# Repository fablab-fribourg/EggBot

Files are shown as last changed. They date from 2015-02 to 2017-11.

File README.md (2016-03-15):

# EggBot
All you need to make your own EggBot.

This repository contains the Arduino code and a computer application to print files.

## Licence

 * Hardware is under Creative Commons Attribution-ShareAlike 3.0
 * Arduino code is under GNU GPL
 * The GcodeSender (computer application) application is under MIT Licence
 
## Electronics 
 * 1x Arduino uno
 * 1x CNC shield for Arduino UNO
 * 2x A4988 Stepper driver
 * 2x Nema 17 Stepper motor
 * 1x mini servo
 * 1x 12 volt power supply (min 1A)
 * 6x Jumpers

##Mechanic
 * 8x	Nuts M4
 * 1x	Threaded shaft M4 100mm
 * 8x	Hex head screws M4 x20mm
 * 20x	Nuts M3
 * 16x	Screws M3 x 8mm
 * 12x	Screws M3 x 16mm
 * 8x	Washers M3
 * 1x	Nail diam 1 or 2mm
 * 1x	Spring ~M4

## Computer application

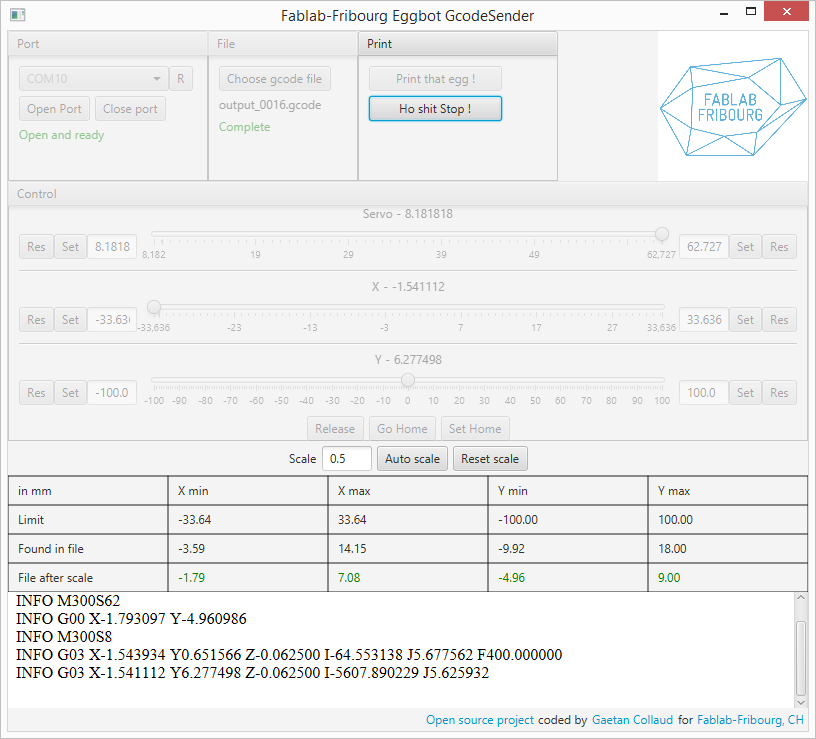
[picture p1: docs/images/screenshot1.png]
GcodeSender


**Steps to print a file**

* start the application
* choose and open the port where the arduino is connected (donc forget to upload the Arduino sketch first)
* choose the file you want to print 
  * this is a simple GCode file
  * you can convert an image with the last version of inkscape ([demo](https://www.youtube.com/watch?v=4jYKMAjzK3A))
* *[Optional]* adjust the limits
* *[Optional]* adjust the scale
* *[Optional]* define home
* "Print that egg"

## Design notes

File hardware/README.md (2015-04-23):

# EggBot Hardware

In this directory you will find the lasercut file to make you own eggbot.

Use the eggbot-frame-fablab-fribourg.svg if you want our upgraded version. Otherwise use the orignal files.

## Licence



Everything in this directory is under Creative Commons Attribution-ShareAlike 3.0.

Original work is from [Christoph Reinhardt](http://www.christophreinhardt.ch/)

Changes made by [Michel Collaud](http://www.easyloc.ch/) :
 * machine height
 * pen support
 * electronic position
 * holes adjustments
 * laser cutter optimisations

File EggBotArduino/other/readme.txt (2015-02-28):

v0.1

This is the firmware for an EggBot-style SphereBot.
The firmware directly interprets GCode send over the serial port.

There will be more information on the SphereBot at http://pleasantsoftware.com/developer/3d (in the near future...)

!!!!!!!!
This sketch needs the following non-standard libraries (install them in the Arduino library directory):
SoftwareServo: http://www.arduino.cc/playground/ComponentLib/Servo
TimerOne: http://www.arduino.cc/playground/Code/Timer1
!!!!!!!!

Copyright 2011 by Eberhard Rensch <http://pleasantsoftware.com/developer/3d>

This program is free software: you can redistribute it and/or modify
it under the terms of the GNU General Public License as published by
the Free Software Foundation, either version 3 of the License, or
(at your option) any later version.

This program is distributed in the hope that it will be useful,
but WITHOUT ANY WARRANTY; without even the implied warranty of
MERCHANTABILITY or FITNESS FOR A PARTICULAR PURPOSE.  See the
GNU General Public License for more details.

You should have received a copy of the GNU General Public License
along with this program.  If not, see <http://www.gnu.org/licenses/>

Part of this code is based on/inspired by the Helium Frog Delta Robot Firmware
by Martin Price <http://www.HeliumFrog.com>

To create tags File: ctags --langmap="C++:+.pde" S*

GCode commands:

G90	Absolut modus
G91	Icremental modus:

M300S0	Servo 0 degree
M300S90	Servo 90 degree

M18	Stepper off

G0X0Y40	Rapid movement (pen 0mm, rotation 40mm)
G1X40Y0 Slower movement (pen 40mm, rotation 0mm)
G1Y10F660 Movement with feed 660mm/s (rotation 10mm)

;	Comment
( .. )	Comment

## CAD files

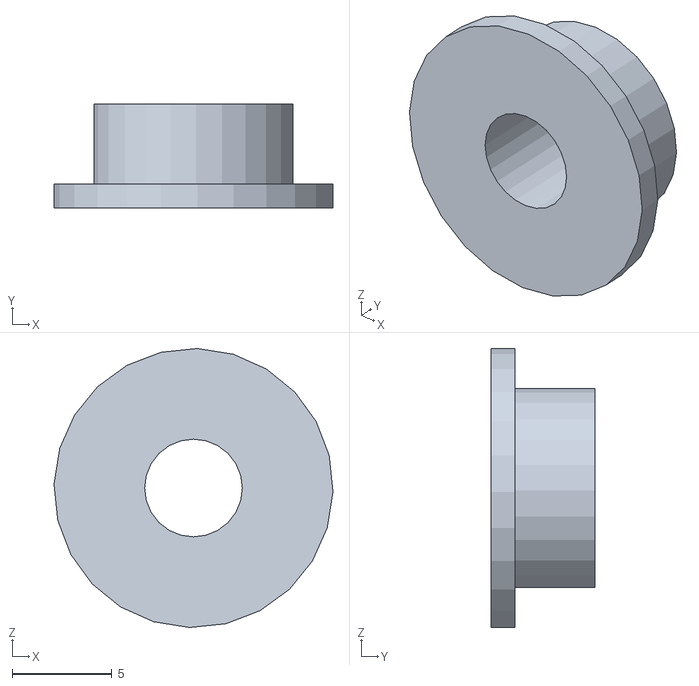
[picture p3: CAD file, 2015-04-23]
hardware/3d_printer/christophreinhardt/douille.stl
14.0 x 5.20 x 14.0

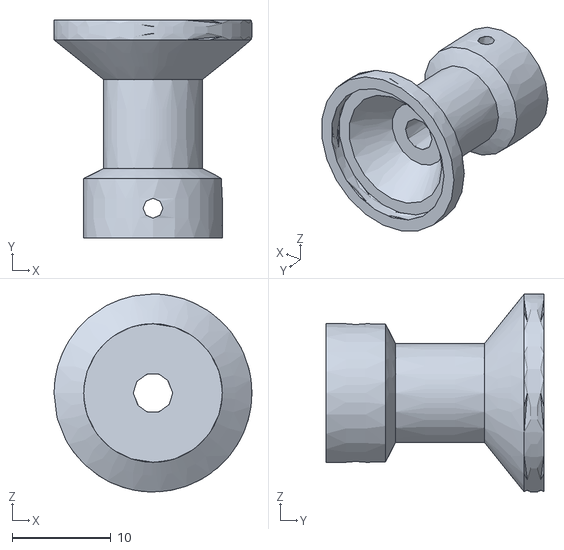
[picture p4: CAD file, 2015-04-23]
hardware/3d_printer/Michel/SupportRondelleCaoutchouc.stl
20.0 x 22.0 x 20.0

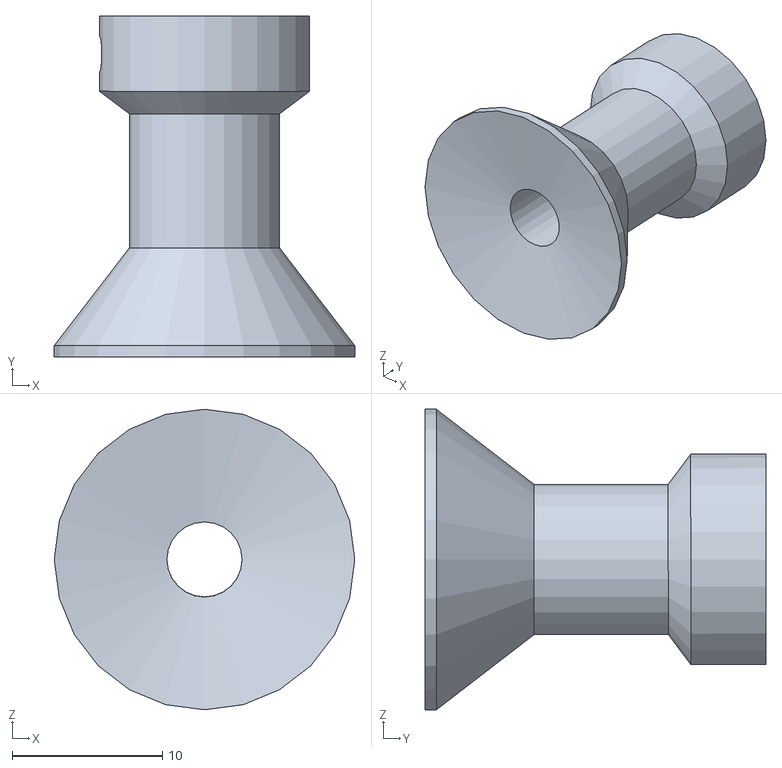
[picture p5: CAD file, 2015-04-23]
hardware/3d_printer/christophreinhardt/supportoeuf.stl
20.0 x 22.7 x 20.0

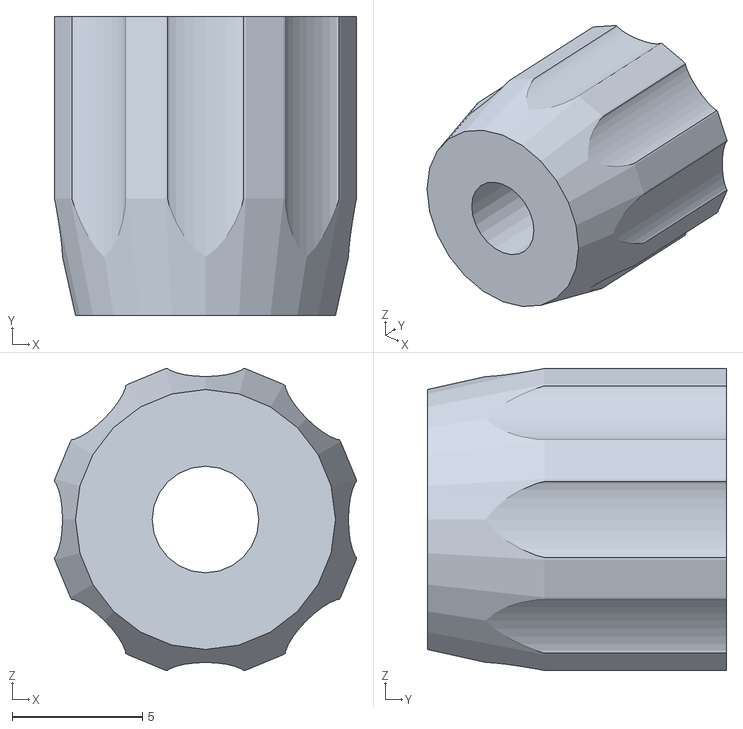
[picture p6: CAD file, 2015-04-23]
hardware/3d_printer/christophreinhardt/M4.stl
11.6 x 11.5 x 11.6

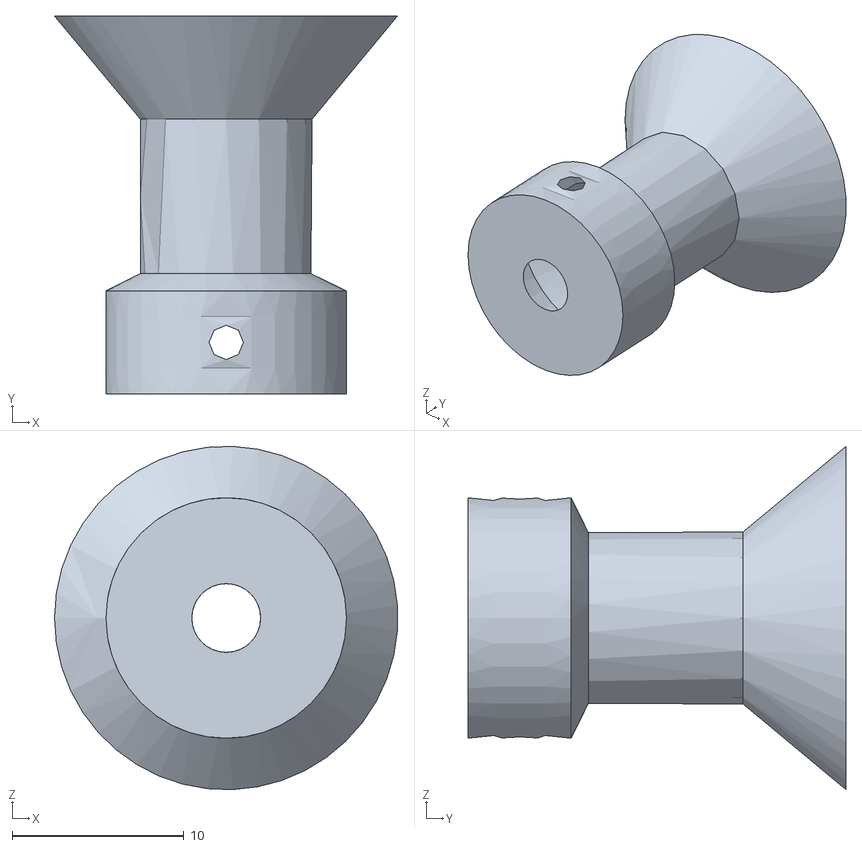
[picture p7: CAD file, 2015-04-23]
hardware/3d_printer/Michel/Support1.stl
20.0 x 22.0 x 20.0

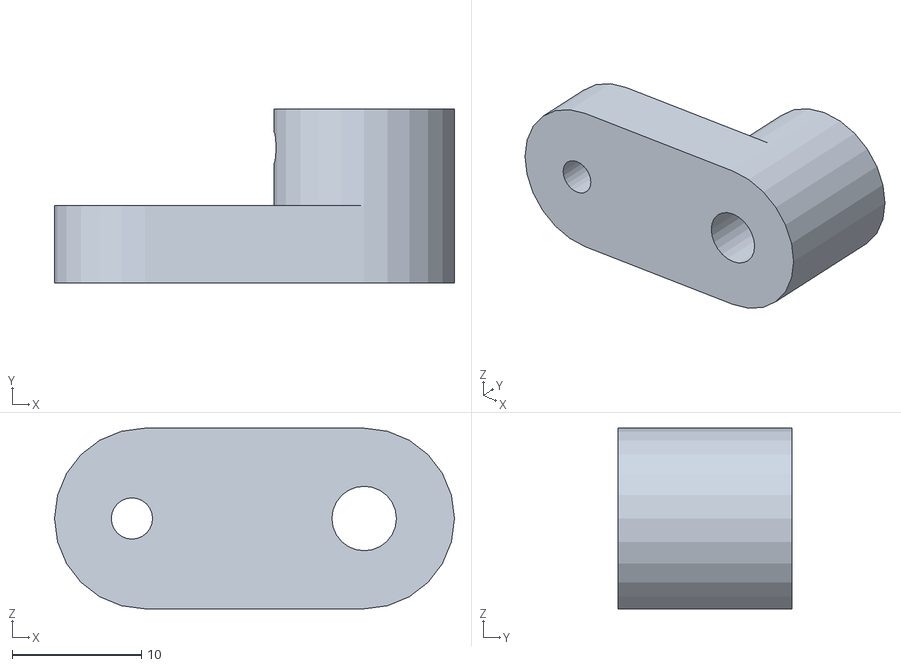
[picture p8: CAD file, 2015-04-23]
hardware/3d_printer/christophreinhardt/entrainement.stl
31.0 x 13.5 x 14.0

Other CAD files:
hardware/3d_printer/Michel/SupportOring.stl

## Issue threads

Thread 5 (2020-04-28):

Please more documentation

ralfsteck, 2020-04-28:
I try to get my eggbot up and running for weeks now. I understand that the directory GCode Sender contains the source code of the application. But how to compile this? What is the main file?

I have experiences in building my own 3D printers and CNC mills, but this breaks my knowledge.

gaetancollaud, 2020-04-28:
Just use a released binary, no need to compile => https://github.com/fablab-fribourg/EggBot/releases

ralfsteck, 2020-04-28:
Oh wow. I always missd this. Thanks alot. I will start trying it this afternoon.

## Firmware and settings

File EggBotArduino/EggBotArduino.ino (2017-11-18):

/*
 * Copyright 2011 by Eberhard Rensch <http://pleasantsoftware.com/developer/3d>
 *
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
 * Part of this code is based on/inspired by the Helium Frog Delta Robot Firmware
 * by Martin Price <http://www.HeliumFrog.com>
 *
 * !!!!!!!!
 * This sketch needs the following non-standard libraries (install them in the Arduino library directory):
 * SoftwareServo: http://www.arduino.cc/playground/ComponentLib/Servo
 * TimerOne: http://www.arduino.cc/playground/Code/Timer1
 * !!!!!!!!
 */

#include "EggTimerOne.h"
#include "EggSoftwareServo.h"
#include "StepperModel.h"


#define TIMER_DELAY 64

/*
 * PINS
 */

#define XAXIS_DIR_PIN 5
#define XAXIS_STEP_PIN 2
#define XAXIS_ENABLE_PIN 8
#define XAXIS_ENDSTOP_PIN -1

#define YAXIS_DIR_PIN 6
#define YAXIS_STEP_PIN 3
#define YAXIS_ENABLE_PIN 8
#define YAXIS_ENDSTOP_PIN -1 // <0 0> No Endstop!

#define SERVO_PIN 4

/*
 * Other Configuration
 */

#define DEFAULT_PEN_UP_POSITION 30
#define XAXIS_MIN_STEPCOUNT -300
#define XAXIS_MAX_STEPCOUNT 300
#define DEFAULT_ZOOM_FACTOR 1. // With a Zoom-Faktor of .65, I can print gcode for Makerbot Unicorn without changes. 
// The zoom factor can be also manipulated by the propretiary code M402
#define SERVO_REVERSE 0  // Set to 1 if your servo is mounted the other way around

/* --------- */

StepperModel xAxisStepper(XAXIS_DIR_PIN, XAXIS_STEP_PIN, XAXIS_ENABLE_PIN, XAXIS_ENDSTOP_PIN,
		XAXIS_MIN_STEPCOUNT, XAXIS_MAX_STEPCOUNT, 200.0, 16);
StepperModel rotationStepper(YAXIS_DIR_PIN, YAXIS_STEP_PIN, YAXIS_ENABLE_PIN, YAXIS_ENDSTOP_PIN,
		0, 0, 200.0, 16);

SoftwareServo servo;
boolean servoEnabled = true;

long intervals = 0;
volatile long intervals_remaining = 0;
volatile boolean isRunning = false;

// comm variables
const int MAX_CMD_SIZE = 296;
char buffer[MAX_CMD_SIZE]; // buffer for serial commands
char serial_char; // value for each byte read in from serial comms
int serial_count = 0; // current length of command
char *strchr_pointer; // just a pointer to find chars in the cmd string like X, Y, Z, E, etc
boolean comment_mode = false;
// end comm variables

// GCode States
double currentOffsetX = 0.;
double currentOffsetY = 0.;
boolean absoluteMode = true;
double feedrate = 2000.; // mm/minute
double zoom = DEFAULT_ZOOM_FACTOR;

const double maxFeedrate = 6000.;
// ------

void setup() {
	Serial.begin(115200);

	clear_buffer();

	servo.attach(SERVO_PIN);
	servo.write(DEFAULT_PEN_UP_POSITION);

	if (servoEnabled) {
		for (int i = 0; i < 100; i++) {
			SoftwareServo::refresh();
			delay(4);
		}
	}

	//--- Activate the PWM timer
	Timer1.initialize(TIMER_DELAY); // Timer for updating pwm pins
	Timer1.attachInterrupt(doInterrupt);

	//#ifdef AUTO_HOMING
	//    xAxisStepper.autoHoming();
	//    xAxisStepper.setTargetPosition(0.);
	//    commitSteppers(maxFeedrate);
	//    delay(2000);
	//    xAxisStepper.enableStepper(false);
	//#endif


	Serial.println("ready");
}

void loop() // input loop, looks for manual input and then checks to see if and serial commands are coming in
{
	get_command(); // check for Gcodes
	if (servoEnabled)
		SoftwareServo::refresh();
}

//--- Interrupt-Routine: Move the steppers

void doInterrupt() {
	if (isRunning) {
		if (intervals_remaining-- == 0)
			isRunning = false;
		else {
			rotationStepper.doStep(intervals);
			xAxisStepper.doStep(intervals);
		}
	}
}

void commitSteppers(double speedrate) {
	long deltaStepsX = xAxisStepper.delta;
	if (deltaStepsX != 0L) {
		xAxisStepper.enableStepper(true);
	}

	long deltaStepsY = rotationStepper.delta;
	if (deltaStepsY != 0L) {
		rotationStepper.enableStepper(true);
	}
	long masterSteps = (deltaStepsX > deltaStepsY) ? deltaStepsX : deltaStepsY;

	double deltaDistanceX = xAxisStepper.targetPosition - xAxisStepper.getCurrentPosition();
	double deltaDistanceY = rotationStepper.targetPosition - rotationStepper.getCurrentPosition();

	// how long is our line length?
	double distance = sqrt(deltaDistanceX * deltaDistanceX + deltaDistanceY * deltaDistanceY);

	// compute number of intervals for this move
	double sub1 = (60000. * distance / speedrate);
	double sub2 = sub1 * 1000.;
	intervals = (long) sub2 / TIMER_DELAY;

	intervals_remaining = intervals;
	const long negative_half_interval = -intervals / 2;

	rotationStepper.counter = negative_half_interval;
	xAxisStepper.counter = negative_half_interval;

	//  Serial.print("Speedrate:");
	//  Serial.print(speedrate, 6);
	//  Serial.print(" dX:");
	//  Serial.print(deltaStepsX);
	//  Serial.print(" dY:");
	//  Serial.print(deltaStepsY);
	//  Serial.print(" masterSteps:");
	//  Serial.print(masterSteps);
	//  Serial.print(" dDistX:");
	//  Serial.print(deltaDistanceX);
	//  Serial.print(" dDistY:");	
	//  Serial.print(deltaDistanceY);
	//  Serial.print(" distance:");
	//  Serial.print(distance);
	//  Serial.print(" sub1:");
	//  Serial.print(sub1, 6);
	//  Serial.print(" sub2:");
	//  Serial.print(sub2, 6);
	//  Serial.print(" intervals:");
	//  Serial.print(intervals);
	//  Serial.print(" negative_half_interval:");
	//  Serial.println(negative_half_interval);
	//  Serial.print("Y currentStepCount:");
	//  Serial.print(rotationStepper.currentStepcount);
	//  Serial.print(" targetStepCount:");
	//  Serial.println(rotationStepper.targetStepcount);

	isRunning = true;
}

void get_command() // gets commands from serial connection and then calls up subsequent functions to deal with them
{
	if (!isRunning && Serial.available() > 0) // each time we see something
	{
		serial_char = Serial.read(); // read individual byte from serial connection

		if (serial_char == '\n' || serial_char == '\r') // end of a command character
		{
			buffer[serial_count] = 0;
			process_commands(buffer, serial_count);
			clear_buffer();
			comment_mode = false; // reset comment mode before each new command is processed
		} else // not end of command
		{
			if (serial_char == ';' || serial_char == '(') // semicolon signifies start of comment
			{
				comment_mode = true;
			}

			if (comment_mode != true) // ignore if a comment has started
			{
				buffer[serial_count] = serial_char; // add byte to buffer string
				serial_count++;
				if (serial_count > MAX_CMD_SIZE) // overflow, dump and restart
				{
					clear_buffer();
					Serial.flush();
				}
			}
		}
	}
}

void clear_buffer() // empties command buffer from serial connection
{
	serial_count = 0; // reset buffer placement
}

boolean getValue(char key, char command[], double* value) {
	// find key parameter
	strchr_pointer = strchr(buffer, key);
	if (strchr_pointer != NULL) // We found a key value
	{
		*value = (double) strtod(&command[strchr_pointer - command + 1], NULL);
		return true;
	}
	return false;
}

void process_commands(char command[], int command_length) // deals with standardized input from serial connection
{
	if (command_length > 0 && command[0] == 'G') // G code
	{
		int codenum = (int) strtod(&command[1], NULL);

		double tempX = xAxisStepper.getCurrentPosition();
		double tempY = rotationStepper.getCurrentPosition();

		double xVal;
		boolean hasXVal = getValue('X', command, &xVal);
		if (hasXVal) xVal *= zoom;
		double yVal;
		boolean hasYVal = getValue('Y', command, &yVal);
		if (hasYVal) yVal *= zoom;
		double iVal;
		boolean hasIVal = getValue('I', command, &iVal);
		if (hasIVal) iVal *= zoom;
		double jVal;
		boolean hasJVal = getValue('J', command, &jVal);
		if (hasJVal) jVal *= zoom;
		double rVal;
		boolean hasRVal = getValue('R', command, &rVal);
		if (hasRVal) rVal *= zoom;
		double pVal;
		boolean hasPVal = getValue('P', command, &pVal);

		getValue('F', command, &feedrate);

		xVal += currentOffsetX;
		yVal += currentOffsetY;

		if (absoluteMode) {
			if (hasXVal)
				tempX = xVal;
			if (hasYVal)
				tempY = yVal;
		} else {
			if (hasXVal)
				tempX += xVal;
			if (hasYVal)
				tempY += yVal;
		}

		switch (codenum) {
			case 0: // G0, Rapid positioning
				xAxisStepper.setTargetPosition(tempX);
				rotationStepper.setTargetPosition(tempY);
				commitSteppers(maxFeedrate);
				break;
			case 1: // G1, linear interpolation at specified speed
				xAxisStepper.setTargetPosition(tempX);
				rotationStepper.setTargetPosition(tempY);
				commitSteppers(feedrate);
				break;
			case 2: // G2, Clockwise arc
			case 3: // G3, Counterclockwise arc
				if (hasIVal && hasJVal) {
					double centerX = xAxisStepper.getCurrentPosition() + iVal;
					double centerY = rotationStepper.getCurrentPosition() + jVal;
					drawArc(centerX, centerY, tempX, tempY, (codenum == 2));
				} else if (hasRVal) {
					//drawRadius(tempX, tempY, rVal, (codenum==2));
				}
				break;
			case 4: // G4, Delay P ms
				if (hasPVal) {
					unsigned long endDelay = millis()+ (unsigned long) pVal;
					while (millis() < endDelay) {
						delay(1);
						if (servoEnabled)
							SoftwareServo::refresh();
					}
				}
				break;
			case 90: // G90, Absolute Positioning
				absoluteMode = true;
				break;
			case 91: // G91, Incremental Positioning
				absoluteMode = false;
				break;
		}
	} else if (command_length > 0 && command[0] == 'M') // M code
	{
		double value;
		int codenum = (int) strtod(&command[1], NULL);
		switch (codenum) {
			case 18: // Disable Drives
				xAxisStepper.resetStepper();
				rotationStepper.resetStepper();
				break;
			case 19: // set current position to home
				xAxisStepper.resetPosition();
				rotationStepper.resetPosition();
				break;
				
			case 300: // Servo Position
				if (getValue('S', command, &value)) {
					servoEnabled = true;
					if (value < 0.)
						value = 0.;
					else if (value > 180.) {
						value = DEFAULT_PEN_UP_POSITION;
						servo.write((int) value);
						for (int i = 0; i < 100; i++) {
							SoftwareServo::refresh();
							delay(4);
						}
						servoEnabled = false;
					}
					// Slow servo down
					while (servo.read() != value){
						if ((servo.read() < value) ^ SERVO_REVERSE){
							servo.write((int) servo.read()+1-2*SERVO_REVERSE);
							for (int i = 0; i < 10; i++) {
							  SoftwareServo::refresh();
							  delay(4);
							}
						}
						else{
							servo.write((int) value);
							SoftwareServo::refresh();
						} 
					}
				}
				break;

			case 400: // Propretary: Reset X-Axis-Stepper settings to new object diameter
				if (getValue('S', command, &value)) {
					xAxisStepper.resetSteppersForObjectDiameter(value);
					xAxisStepper.setTargetPosition(0.);
					commitSteppers(maxFeedrate);
					delay(2000);
					xAxisStepper.enableStepper(false);
				}
				break;

			case 401: // Propretary: Reset Y-Axis-Stepper settings to new object diameter
				if (getValue('S', command, &value)) {
					rotationStepper.resetSteppersForObjectDiameter(value);
					rotationStepper.setTargetPosition(0.);
					commitSteppers(maxFeedrate);
					delay(2000);
					rotationStepper.enableStepper(false);
				}
				break;

			case 402: // Propretary: Set global zoom factor
				if (getValue('S', command, &value)) {
					zoom = value;
				}

		}
	}

	// done processing commands
	if (Serial.available() <= 0) {
		Serial.print("ok:");
		Serial.println(command);
	}
}

/* This code was ported from the Makerbot/ReplicatorG java sources */
void drawArc(double centerX, double centerY, double endpointX, double endpointY, boolean clockwise) {
	// angle variables.
	double angleA;
	double angleB;
	double angle;
	double radius;
	double length;

	// delta variables.
	double aX;
	double aY;
	double bX;
	double bY;

	// figure out our deltas
	double currentX = xAxisStepper.getCurrentPosition();
	double currentY = rotationStepper.getCurrentPosition();
	aX = currentX - centerX;
	aY = currentY - centerY;
	bX = endpointX - centerX;
	bY = endpointY - centerY;

	// Clockwise
	if (clockwise) {
		angleA = atan2(bY, bX);
		angleB = atan2(aY, aX);
	}// Counterclockwise
	else {
		angleA = atan2(aY, aX);
		angleB = atan2(bY, bX);
	}

	// Make sure angleB is always greater than angleA
	// and if not add 2PI so that it is (this also takes
	// care of the special case of angleA == angleB,
	// ie we want a complete circle)
	if (angleB <= angleA)
		angleB += 2. * M_PI;
	angle = angleB - angleA;

	// calculate a couple useful things.
	radius = sqrt(aX * aX + aY * aY);
	length = radius * angle;

	// for doing the actual move.
	int steps;
	int s;
	int step;

	// Maximum of either 2.4 times the angle in radians
	// or the length of the curve divided by the curve section constant
	steps = (int) ceil(max(angle * 2.4, length));

	// this is the real draw action.
	double newPointX = 0.;
	double newPointY = 0.;

	for (s = 1; s <= steps; s++) {
		// Forwards for CCW, backwards for CW
		if (!clockwise)
			step = s;
		else
			step = steps - s;

		// calculate our waypoint.
		newPointX = centerX + radius * cos(angleA + angle * ((double) step / steps));
		newPointY = centerY + radius * sin(angleA + angle * ((double) step / steps));

		// start the move
		xAxisStepper.setTargetPosition(newPointX);
		rotationStepper.setTargetPosition(newPointY);
		commitSteppers(feedrate);

		while (isRunning) {
			delay(1);
			if (servoEnabled)
				SoftwareServo::refresh();
		};
	}
}

/* Make life easier for vim users */
/* vim:set filetype=cpp: */

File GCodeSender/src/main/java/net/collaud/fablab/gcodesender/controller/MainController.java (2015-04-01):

package net.collaud.fablab.gcodesender.controller;

import java.awt.Desktop;
import java.io.File;
import java.io.IOException;
import java.net.URI;
import java.net.URISyntaxException;
import java.net.URL;
import java.util.Arrays;
import java.util.LinkedList;
import java.util.List;
import java.util.Optional;
import java.util.ResourceBundle;
import javafx.application.Platform;
import javafx.beans.binding.BooleanBinding;
import javafx.beans.property.BooleanProperty;
import javafx.beans.property.ObjectProperty;
import javafx.beans.property.SimpleBooleanProperty;
import javafx.beans.property.SimpleObjectProperty;
import javafx.beans.value.ObservableValue;
import javafx.collections.FXCollections;
import javafx.fxml.FXML;
import javafx.fxml.Initializable;
import javafx.scene.control.Button;
import javafx.scene.control.ComboBox;
import javafx.scene.control.Label;
import javafx.scene.control.TitledPane;
import javafx.scene.control.Tooltip;
import javafx.scene.layout.HBox;
import javafx.scene.paint.Color;
import javafx.scene.web.WebView;
import javafx.stage.FileChooser;
import javafx.stage.Stage;
import lombok.Setter;
import lombok.extern.slf4j.Slf4j;
import net.collaud.fablab.gcodesender.config.Config;
import net.collaud.fablab.gcodesender.config.ConfigKey;
import net.collaud.fablab.gcodesender.gcode.GcodeFileService;
import net.collaud.fablab.gcodesender.gcode.GcodeFileStatus;
import net.collaud.fablab.gcodesender.gcode.GcodeNotifyMessage;
import net.collaud.fablab.gcodesender.gcode.GcodeService;
import net.collaud.fablab.gcodesender.serial.PortStatus;
import static net.collaud.fablab.gcodesender.serial.PortStatus.ERROR;
import static net.collaud.fablab.gcodesender.serial.PortStatus.NOT_RESPONDING;
import static net.collaud.fablab.gcodesender.serial.PortStatus.OPEN;
import net.collaud.fablab.gcodesender.serial.SerialPortDefinition;
import net.collaud.fablab.gcodesender.serial.SerialService;
import org.springframework.beans.factory.annotation.Autowired;
import org.springframework.beans.factory.config.ConfigurableBeanFactory;
import org.springframework.context.annotation.Scope;
import org.springframework.stereotype.Controller;

//FIXME persit lastDirectory and port
@Controller
@Scope(ConfigurableBeanFactory.SCOPE_PROTOTYPE)
@Slf4j
public class MainController implements Initializable {

	@Autowired
	private SerialService serialService;

	@Autowired
	private GcodeFileService gcodeFileService;

	@Autowired
	private GcodeService gcodeService;

	@Autowired
	private Config config;

	@Setter
	private Stage stage;

	@FXML
	private Label labelFile;

	@FXML
	private Label labelFileStatus;

	@FXML
	private Button buttonReloadPort;

	@FXML
	private Button buttonOpenPort;

	@FXML
	private Button buttonClosePort;

	@FXML
	private Label labelPortStatus;

	@FXML
	private Button buttonPrintStart;

	@FXML
	private Button buttonPrintStop;

	@FXML
	private ComboBox<SerialPortDefinition> comboPort;

	@FXML
	private WebView htmlLog;

	@FXML
	private TitledPane panePort;

	@FXML
	private TitledPane paneFile;

	@FXML
	private TitledPane panePrint;

	@FXML
	private TitledPane controlPane;

	@FXML
	private HBox manualGCodePane;

	@FXML
	private ControlController controlPaneController;

	@FXML
	private ScalePanelController scalePaneController;

	private final ObjectProperty<File> selectedFile = new SimpleObjectProperty<>();
	private final List<String> logLines = new LinkedList<>();
	private ObjectProperty<SerialPortDefinition> selectedPort;
	private final BooleanProperty printing = new SimpleBooleanProperty(false);
	private File lastDirectory;

	@FXML
	private void reloadPorts() {
		final List<SerialPortDefinition> list = serialService.getListPorts();
		comboPort.setItems(FXCollections.observableArrayList(list));
		Optional<String> last = Optional.ofNullable(config.getProperty(ConfigKey.LAST_PORT));
		SerialPortDefinition value = null;
		if (last.isPresent()) {
			final Optional<SerialPortDefinition> find = list.stream()
					.filter(e -> e.getName().equals(last.get()))
					.findFirst();
			if (find.isPresent()) {
				value = find.get();
			}
		}
		selectedPort.setValue(value);
	}

	@FXML
	private void openPort() {
		serialService.openPort(comboPort.getValue());
	}

	@FXML
	private void closePort() {
		serialService.closePort();
	}

	@FXML
	private void chooseGCodeFile() {
		FileChooser fileChooser = new FileChooser();
		if (lastDirectory != null && lastDirectory.exists()) {
			fileChooser.setInitialDirectory(lastDirectory);
		}
		fileChooser.setTitle("Open GCode file");
		addGCodeExtensionFilter(fileChooser);
		File f = fileChooser.showOpenDialog(stage);
		selectedFile.setValue(f);
		gcodeFileService.analyseFile(f);
	}

	private void addGCodeExtensionFilter(FileChooser fileChooser) {
		fileChooser.getExtensionFilters().add(new FileChooser.ExtensionFilter("Gcode file", 
				Arrays.asList(new String[]{"*.gcode", "*.ngc", "*.nc", "*.tap"})));
		fileChooser.getExtensionFilters().add(new FileChooser.ExtensionFilter("All ", "*.*"));
	}

	@FXML
	private void print() {
		log.info("Print file {} on port {}", selectedFile.get().getAbsolutePath(), selectedPort.get());
		gcodeService.print(scalePaneController.getScaleValue().doubleValue());
		logLines.clear();
		printing.set(true);
	}

	@FXML
	private void stopPrint() {
		log.info("Stop print");
		printing.setValue(false);
		gcodeService.stopPrint();
	}

	@FXML
	private void linkProject() {
		goToLink("https://github.com/fablab-fribourg/EggBot");
	}

	@FXML
	private void linkGaetan() {
		goToLink("http://collaud.net");
	}

	@FXML
	private void linkFablab() {
		goToLink("http://fablab-fribourg.ch/");
	}

	private void goToLink(String url) {
		try {
			Desktop.getDesktop().browse(new URI(url));
		} catch (IOException | URISyntaxException ex) {
			log.error("Cannot open brower for link " + url, ex);
		}
	}
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

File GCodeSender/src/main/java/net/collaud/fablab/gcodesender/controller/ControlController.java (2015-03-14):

package net.collaud.fablab.gcodesender.controller;

import java.net.URL;
import java.util.Map;
import java.util.Optional;
import java.util.ResourceBundle;
import java.util.concurrent.ConcurrentHashMap;
import java.util.concurrent.Semaphore;
import javafx.beans.property.DoubleProperty;
import javafx.beans.value.ChangeListener;
import javafx.beans.value.ObservableValue;
import javafx.fxml.FXML;
import javafx.fxml.Initializable;
import lombok.Getter;
import lombok.extern.slf4j.Slf4j;
import net.collaud.fablab.gcodesender.config.Config;
import net.collaud.fablab.gcodesender.config.ConfigKey;
import net.collaud.fablab.gcodesender.controller.model.LimitsProperty;
import net.collaud.fablab.gcodesender.gcode.GcodeConverterService;
import net.collaud.fablab.gcodesender.gcode.GcodeService;
import net.collaud.fablab.gcodesender.gcode.Motor;
import org.springframework.beans.factory.annotation.Autowired;
import org.springframework.beans.factory.config.ConfigurableBeanFactory;
import org.springframework.context.annotation.Scope;
import org.springframework.stereotype.Controller;

/**
 * FXML Controller class
 *
 * @author Gaetan Collaud
 */
@Controller
@Scope(ConfigurableBeanFactory.SCOPE_PROTOTYPE)
@Slf4j
public class ControlController implements Initializable {

	@Autowired
	private GcodeService gcodeService;

	@Autowired
	private GcodeConverterService gcodeConverterService;

	@Autowired
	private Config config;

	@FXML
	private LinearControlController servoController;

	@Getter
	@FXML
	private LinearControlController xController;

	@Getter
	@FXML
	private LinearControlController yController;

	private final Semaphore semNewValue = new Semaphore(0);
	private final Map<Motor, Double> changedValue = new ConcurrentHashMap<>();

	private ChangeThread changeThread;

	private LimitsProperty limits;

	@Override
	public void initialize(URL url, ResourceBundle rb) {
		changeThread = new ChangeThread();
		changeThread.start();

		servoController.init("Servo", config.getDoubleProperty(ConfigKey.LAST_SERVO_MIN), config.getDoubleProperty(ConfigKey.LAST_SERVO_MAX), 0, 90);
		xController.init("X", config.getDoubleProperty(ConfigKey.LAST_X_MIN), config.getDoubleProperty(ConfigKey.LAST_X_MAX), -40, 40);
		yController.init("Y", config.getDoubleProperty(ConfigKey.LAST_Y_MIN), config.getDoubleProperty(ConfigKey.LAST_Y_MAX), -100, 100);

		servoController.addListener((ObservableValue<? extends Number> observable, Number oldValue, Number newValue) -> {
			changedValue.put(Motor.PEN, newValue.doubleValue());
			semNewValue.release();
		});

		xController.addListener((ObservableValue<? extends Number> observable, Number oldValue, Number newValue) -> {
			changedValue.put(Motor.X, newValue.doubleValue());
			semNewValue.release();
		});

		yController.addListener((ObservableValue<? extends Number> observable, Number oldValue, Number newValue) -> {
			changedValue.put(Motor.Y, newValue.doubleValue());
			semNewValue.release();
		});

		servoController.getMin().addListener((ObservableValue<? extends Number> observable, Number oldValue, Number newValue) -> {
			gcodeConverterService.setServoMin(newValue.doubleValue());
		});
		servoController.getMax().addListener((ObservableValue<? extends Number> observable, Number oldValue, Number newValue) -> {
			gcodeConverterService.setServoMax(newValue.doubleValue());
		});
		gcodeConverterService.setServoMin(servoController.getMin().get());
		gcodeConverterService.setServoMax(servoController.getMax().get());

		limits = new LimitsProperty(xController.getMin(), xController.getMax(), yController.getMin(), yController.getMax());

		//Config bind
		linkConfigSave(ConfigKey.LAST_SERVO_MIN, servoController.getMin());
		linkConfigSave(ConfigKey.LAST_SERVO_MAX, servoController.getMax());
		linkConfigSave(ConfigKey.LAST_X_MIN, xController.getMin());
		linkConfigSave(ConfigKey.LAST_X_MAX, xController.getMax());
		linkConfigSave(ConfigKey.LAST_Y_MIN, yController.getMin());
		linkConfigSave(ConfigKey.LAST_Y_MAX, yController.getMax());

		//realtime binding
		gcodeService.getCurrentPositionServo().addListener((ObservableValue<? extends Number> observable, Number oldValue, Number newValue) -> {
			servoController.setValue(newValue.doubleValue());
		});
		gcodeService.getCurrentPositionX().addListener((ObservableValue<? extends Number> observable, Number oldValue, Number newValue) -> {
			xController.setValue(newValue.doubleValue());
		});
		gcodeService.getCurrentPositionY().addListener((ObservableValue<? extends Number> observable, Number oldValue, Number newValue) -> {
			yController.setValue(newValue.doubleValue());
		});
	}

	private void linkConfigSave(ConfigKey key, DoubleProperty property) {
		property.addListener((ObservableValue<? extends Number> observable, Number oldValue, Number newValue) -> {
			config.setProperty(key, newValue);
		});
	}

	@FXML
	private void actionRelease() {
		new Thread(gcodeService::release).start();
	}

	@FXML
	private void actionGoHome() {
		new Thread(() -> gcodeService.goHome(servoController.getMax().get())).start();
	}

	@FXML
	private void actionSetHome() {
		new Thread(gcodeService::setHome).start();
	}

	public class ChangeThread extends Thread {

		@Override
		public void run() {
			while (true) {
				try {
					semNewValue.acquire();
					while (!changedValue.isEmpty()) {
						for (Motor m : Motor.values()) {
							Optional.ofNullable(changedValue.remove(m))
									.ifPresent(v -> gcodeService.move(m, v));
						}
					}

				} catch (InterruptedException ex) {
					log.error("Interrupted", ex);
				}
			}
		}
	}

	public LimitsProperty getLimits() {
		return limits;
	}

}

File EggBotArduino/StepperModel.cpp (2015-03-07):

/*
 * Copyright 2011 by Eberhard Rensch <http://pleasantsoftware.com/developer/3d>
 *
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
 * You should have received a copy of the GNU General Public License
 * along with this program.  If not, see <http://www.gnu.org/licenses/>
 */

#include "StepperModel.h"
#include "Arduino.h"

/*
 * inEnablePin < 0 => No Endstop
 */
StepperModel::StepperModel(int inDirPin, int inStepPin, int inEnablePin, int inEndStopPin,
		long minSC, long maxSC,
		double in_kStepsPerRevolution, int in_kMicroStepping) {
	kStepsPerRevolution = in_kStepsPerRevolution;
	kMicroStepping = in_kMicroStepping;

	dirPin = inDirPin;
	stepPin = inStepPin;
	enablePin = inEnablePin;
	endStopPin = inEndStopPin;

	minStepCount = minSC;
	maxStepCount = maxSC;

	pinMode(dirPin, OUTPUT);
	pinMode(stepPin, OUTPUT);
	pinMode(enablePin, OUTPUT);
	if (endStopPin >= 0)
		pinMode(endStopPin, INPUT);

	digitalWrite(dirPin, LOW);
	digitalWrite(stepPin, LOW);

	currentStepcount = 0;
	targetStepcount = 0;

	steps_per_mm = (int) ((kStepsPerRevolution / (45. * M_PI)) * kMicroStepping + 0.5); // default value for a "normal" egg (45 mm diameter)
	enableStepper(false);
}

void StepperModel::resetSteppersForObjectDiameter(double diameter) {
	// Calculate the motor steps required to move per mm.
	steps_per_mm = (int) ((kStepsPerRevolution / (diameter * M_PI)) * kMicroStepping + 0.5);
	if (endStopPin >= 0) {
#ifdef AUTO_HOMING
		autoHoming();
#endif
		enableStepper(false);
	} else
		resetStepper();
}

long StepperModel::getStepsForMM(double mm) {
	long steps = (long) (steps_per_mm * mm);

	//  Serial.print("steps for ");
	//  Serial.print(mm);
	//  Serial.print(" mm: ");
	//  Serial.println(steps);

	return steps;
}

/* Currently unused */

/*
void StepperModel::setTargetStepcount(long tsc)
{
   targetPosition = (double)tsc/steps_per_mm;
   targetStepcount = tsc;
   delta = targetStepcount-currentStepcount;
   direction = true;
   if (delta != 0) {
	 enableStepper(true);
   }
   if (delta < 0) {
	delta = -delta;
	direction = false;
   }
}*/

void StepperModel::setTargetPosition(double pos) {
	targetPosition = pos;
	targetStepcount = getStepsForMM(targetPosition);
	//Serial.println(targetStepcount);
	delta = targetStepcount - currentStepcount;
	direction = true;
	if (delta != 0) {
		enableStepper(true);
	}
	if (delta < 0) {
		delta = -delta;
		direction = false;
	}
}

double StepperModel::getCurrentPosition() {
	return (double) currentStepcount / steps_per_mm;
}

void StepperModel::enableStepper(bool enabled) {
	digitalWrite(enablePin, !enabled);
}

void StepperModel::resetStepper() {
	this->resetPosition();
	enableStepper(false);
}

void StepperModel::resetPosition() {
	currentStepcount = 0;
	targetStepcount = 0;
	delta = 0;
	enableStepper(true);
}

void StepperModel::doStep(long intervals) {
	counter += delta;
	if (counter >= 0) {
		digitalWrite(dirPin, direction ? HIGH : LOW);
		counter -= intervals;
		if (direction) {
			if (maxStepCount == 0 || currentStepcount <= maxStepCount) {
				digitalWrite(stepPin, HIGH);
				currentStepcount++;
			}
		} else {
			if (minStepCount == 0 || currentStepcount >= minStepCount) {
				digitalWrite(stepPin, HIGH);
				currentStepcount--;
			}
		}
		digitalWrite(stepPin, LOW);
	}
}

#ifdef AUTO_HOMING

void StepperModel::autoHoming() {
	enableStepper(true);
	digitalWrite(dirPin, LOW);

	while (digitalRead(endStopPin)) {
		digitalWrite(stepPin, HIGH);
		digitalWrite(stepPin, LOW);
		delay(1);
	}

	currentStepcount = minStepCount - 16;
}
#endif

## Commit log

2015-02-28 Revert "arduino"
    This reverts commit aac6892f583205b0b6c365215dff27a063aebc07.
    [EggBotArduino.ino, EggSoftwareServo.cpp, EggTimerOne.cpp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]
2015-02-28 Revert "Revert "arduino""
    This reverts commit db738dd2064b3f14ce6020a247eff306c2236fc8.
    [EggBotArduino.ino, EggSoftwareServo.cpp, EggTimerOne.cpp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]
2015-02-28 arduino code change
2015-03-01 Thread sync
2015-03-04 reduce servo waiting time from 400 to 200ms
2015-03-04 servo time to 300ms
2015-03-05 add M19 command to reset home
    [EggBotArduino.ino, StepperModel.cpp]
2015-03-07 home and release button
2015-03-07 enable motor when reset position
    [StepperModel.cpp]
2015-03-14 take servo limit
2015-04-01 servo correction
2015-04-23 3d printed part
    [M4.stl, Support1.stl, SupportOring.stl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]
2017-11-07 Added slow servo down
2017-11-18 servo down changed to handle reversed servos
    [EggBotArduino.ino]
2017-11-18 set reverse to 0 by default
    [EggBotArduino.ino]
